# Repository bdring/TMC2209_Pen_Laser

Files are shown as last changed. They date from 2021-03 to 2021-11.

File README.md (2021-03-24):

# TMC2209 Pen Laser

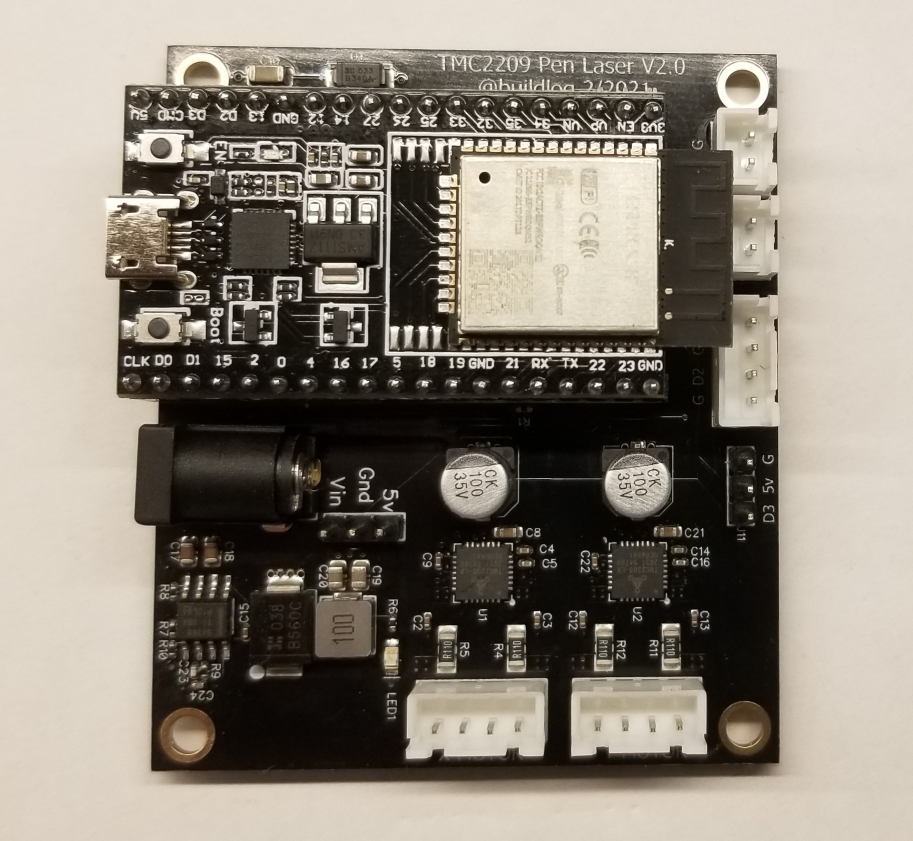
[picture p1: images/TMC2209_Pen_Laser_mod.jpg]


This is a pen plotter controller that uses the ESP32 microcontroller and TMC2209 stepper motors drivers. The ESP32 runs [Grbl_ESP32 firmware](https://github.com/bdring/Grbl_Esp32) which allows you to run your machine wirelessly from your phone or PC via Bluetooth or Wifi. You can also stream via USB or micro SD card. The TMC2209 stepper drivers run your stepper motors super quietly and you can completely configure them via software (no more pots and jumpers).

Features

- (2) Built in TMC2209 Stepper Drivers
  - 12-30V operation
  - 1.2A Max Run Current
  - Sensorless stall detection
  - All settings adjustable in firmware
- (2) Input Circuits
  - Includes R/C Noise filtering
- (1) RC Servo Output
  - For pen lift mechanism
- (2) 5V outputs (typical uses)
  - Laser PWM
  - Laser Enable
  - Assist Air
  - Spindle
- (1) Fan connector
- (1) Micro SD socket.

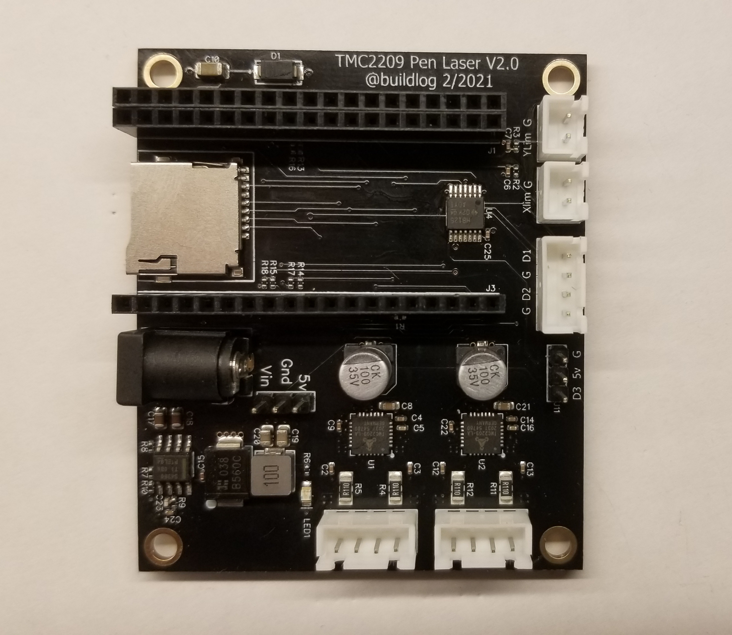
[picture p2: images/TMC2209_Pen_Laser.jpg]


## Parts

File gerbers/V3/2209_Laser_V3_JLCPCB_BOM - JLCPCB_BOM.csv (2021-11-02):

Value | RefDes | Footprint | LCSC P/N
100uF | C1, C11 | SMD-ECAP-6.3x5.3 | C134723
100nF | C2, C3, C4, C6, C7, C9, C12, C13, C14, C15, C22, C25 | 402 | C307331
22nF | C5, C16 | 402 | C1532
4.7uF | C8, C21 | 603 | C69335
10uF 50V | C10 | 1206 | C100122
2.2uF 50V | C17, C18 | 805 | C49217
47uF 6.3V | C19, C20 | 805 | C16780
39pF 50V | C23 | 402 | C106223
6.8nF 50V | C24 | 402 | C152792
40V 3A | D1 | SMA(DO-214AC) | C64982
B560C | D2 | SMC(DO-214AB) | C35722
19S | J1, J2, J3 | Through hole | C319202
3P | J4 | Through hole | C49257
DC Jack | J9 | Through Hole | C84007
 | J7 |  | C84007
10uH | L1 | SMD,5.2x5.4x3.0mm | C408408
GRN | LED1 |  | C84257
 | MH1, MH2, MH3, MH4 | Mounting Hole
10k | R1, R16, R17, R18, R20 | 402 | C60490
100R | R2, R3 | 402 | C106232
0.11R | R4, R5, R11, R12 | 1206 | C247458
2k | R6 | 402 | C4109
270k | R7 | 402 | C25770
100k | R8 | 402 | C25741
13k | R9 | 402 | C25754
51k | R10 | 402 | C25794
1k | R13, R14, R15, R19 | 402 | C11702
Micro SD | SD1 | SD | C91145
4P | TB1, TB2, TB3, TB4, TB5 | Through Hole | C577596
TMC2209 | U1, U2 | QFN-28_EP_5.0x5.0x0.5P | C465949
TPS54360 | U3 | SOP-8_EP_150mil | C44377
AHCT125 | U4 | TSSOP-14_4.4x5.0x0.65P | C36365

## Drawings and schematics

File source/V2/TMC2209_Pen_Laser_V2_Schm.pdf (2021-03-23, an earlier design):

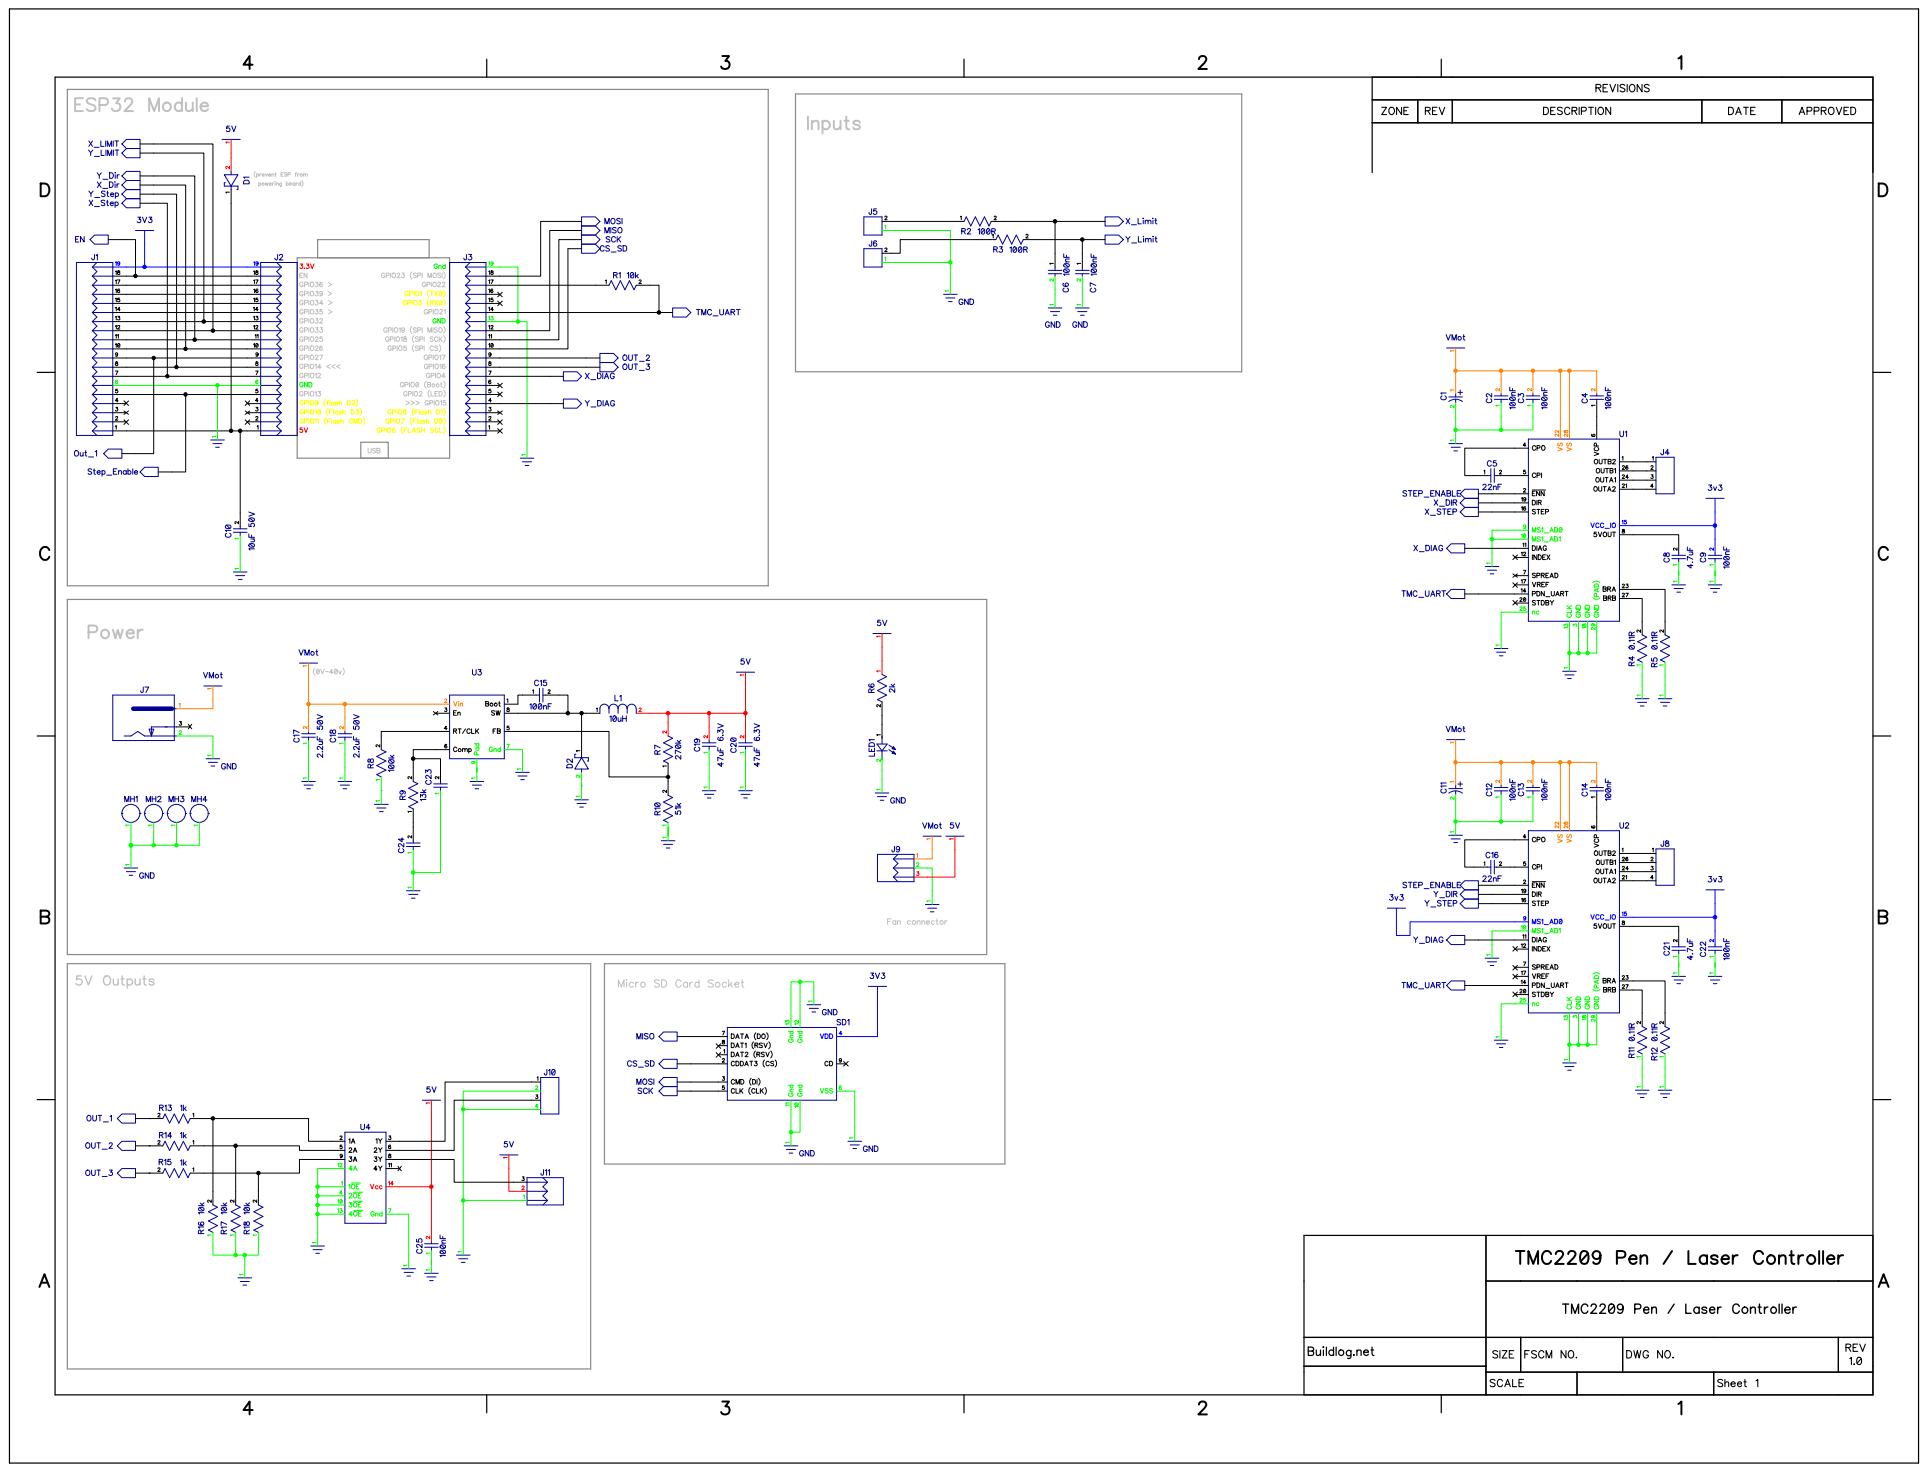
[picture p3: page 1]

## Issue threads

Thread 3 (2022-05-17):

Placement file correct?

Kenitilas, 2022-05-17:
Hey,

I am a real noob so I don't know if this is a issue and how to fix it myself.

Since this board is not available on the German market right now I wanted it to get manufactured. After uploading the files the preview doesn't seem to be right (see picture). Is this a error by the files or by the manufacturers website?

Thanks for the help

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
!

Kenitilas, 2022-05-27:
I ordered the PCB and it was corrected by the shop. I think the placement file is correct. But there is a error in the BOM file.
Position J9 is a second DC-Jack and thus too much for this layout

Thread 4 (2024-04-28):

Buzzing Steppers preventing ESP32 connection

TimKlues, 2024-04-28:
I successfully constructed a SCARA-type sand drawing table using the TMC2209 Pen Laser V2.0 controller board and Grbl ESP32 firmware. After about a year of non-use, I plugged in the controller only to hear the steppers buzzing loudly.  (They were always very quiet).  I could not connect to the ESP32 via ESP3D. I unplugged the steppers and I was able to connect without any issues. As soon as I add the steppers I can’t connect.  I must be overlooking something fundamental but I’m just not seeing it. Do you have any suggestions? I’m trying to avoid re-flashing the firmware which was a major pain for someone with my limited (zero) coding abilities.

bdring, 2024-04-28:
Sorry, Could you open an issue at the FluidNC GitHub repo. It has a template for you to provide the details we need to help you.

https://github.com/bdring/FluidNC/issues

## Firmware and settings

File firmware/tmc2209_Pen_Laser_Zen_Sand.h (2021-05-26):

#pragma once
// clang-format off

/*
    tmc2209_Pen_Laser_Zen_Sand.h
    Part of Grbl_ESP32

    Pin assignments for the TMC2130 Pen/Laser controller
    https://github.com/bdring/Grbl_ESP32_TMC2130_Plotter_Controller

    2021-04-16 B. Dring

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
    You should have received a copy of the GNU General Public License
    along with Grbl_ESP32.  If not, see <http://www.gnu.org/licenses/>.
*/
#define MACHINE_NAME            "TMC2209 Pen/Laser Zen Sand"

#define CUSTOM_CODE_FILENAME    "../Custom/CoreXY.cpp"

#define USE_KINEMATICS      // there are kinematic equations for this machine
#define USE_FWD_KINEMATICS  // report in cartesian
#define USE_MACHINE_INIT    // There is some custom initialization for this machine
#define USE_CUSTOM_HOMING

#define N_AXIS 3

#define TRINAMIC_RUN_MODE           TrinamicMode :: StealthChop // Optional TrinamicMode :: CoolStep or TrinamicMode :: StallGuard
#define TRINAMIC_HOMING_MODE        TrinamicMode :: StealthChop // Optional TrinamicMode :: CoolStep or TrinamicMode :: StallGuard

#define TMC_UART                UART_NUM_1
#define TMC_UART_RX             GPIO_NUM_21
#define TMC_UART_TX             GPIO_NUM_22 

#define X_TRINAMIC_DRIVER       2209
#define X_STEP_PIN              GPIO_NUM_12
#define X_DIRECTION_PIN         GPIO_NUM_26
#define X_RSENSE                TMC2209_RSENSE_DEFAULT
#define X_DRIVER_ADDRESS        0
#define DEFAULT_X_MICROSTEPS    16

#define Y_TRINAMIC_DRIVER       2209
#define Y_STEP_PIN              GPIO_NUM_14
#define Y_DIRECTION_PIN         GPIO_NUM_25
#define Y_RSENSE                TMC2209_RSENSE_DEFAULT
#define Y_DRIVER_ADDRESS        1
#define DEFAULT_Y_MICROSTEPS    16

// OK to comment out to use pin for other features
#define STEPPERS_DISABLE_PIN GPIO_NUM_13

// cooment Z stuff out if you you don't use a Z
#define Z_SERVO_PIN                   GPIO_NUM_16 // Labeled D3 on controller
#define DEFAULT_Z_MAX_TRAVEL          5.0   // Range of travel is 5mm
#define DEFAULT_Z_HOMING_MPOS         5.0   // MPos will be set to 5mm after homing
#define Z_SERVO_CAL_MIN               1.0   // calibration factor for the minimum PWM duty
#define Z_SERVO_CAL_MAX               1.0   // calibration factor for the maximum PWM duty

//#define USE_STALLGUARD_LIMITS  // uncomment to use stallguard as limit switches
#ifdef USE_STALLGUARD_LIMITS
    // StallGuard Limit Pins
    #define X_LIMIT_PIN             GPIO_NUM_4
    #define Y_LIMIT_PIN             GPIO_NUM_15
#else
    // Switch Limit Pins
    #define X_LIMIT_PIN             GPIO_NUM_33
    #define Y_LIMIT_PIN             GPIO_NUM_32
#endif

#define SPINDLE_TYPE                SpindleType::LASER
#define LASER_OUTPUT_PIN            GPIO_NUM_27      // Labeled D1 on controller
#define LASER_ENABLE_PIN            GPIO_NUM_17      // Labeled D2 on controller

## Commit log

2021-03-23 Uploading files
    [2209_Pen_Laser_V2_BOM.xlsx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]
2021-11-01 Adding V3 Source and Gerbers
    [2209_Laser_V3_JLCPCB_BOM - JLCPCB_BOM.csv, 2209_Laser_V3_JLCPCB_Placement - JLCPCB_Placement.csv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]
2021-11-02 Fixed BOM values
    [2209_Laser_V3_JLCPCB_BOM - JLCPCB_BOM.csv]

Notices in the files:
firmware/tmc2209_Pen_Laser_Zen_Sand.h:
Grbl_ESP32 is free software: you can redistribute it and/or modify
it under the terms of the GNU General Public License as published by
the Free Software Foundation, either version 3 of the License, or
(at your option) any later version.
